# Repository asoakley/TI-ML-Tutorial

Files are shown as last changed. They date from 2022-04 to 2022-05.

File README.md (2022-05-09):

# TI-ML-Tutorial
<html>
<body>
<h1>TI Machine Learning Robotics</h1>
<h3>Tutorial repository for TI-RSLK MAX Machine Learning used for NC State ECE Senior Design Fall 2021-Spring 2022</h3>
<ul>
    <li>PCB folder contains Eagle CAD files for the custom PCB schematic file as well as the board file. It also includes the necessary gerbers and libraries needed to recreate the custom sensors PCB</li>
    <ul>
        <li>Eagle Libraries contains the libraries needed to recreate our schematic and board</li>
        <li>PCB Gerbers are the gerber files that can be sent to a manufacturer for printing</li>
    </ul>
    <li>libraries folder contains the libraries used in Arduino IDE to get the MSP432 microcontroller and the RSLK MAX to function. 
    It also contains two pretrained Edge Impulse libraries that we have tested for both Terrrain Recognition and Keyword Recognition</li>
    <li>prediction folder contains the Arduino code for running edge impulse models. 
    It contains code for both Audio and Accelerometer Machine Learning as well as a template code for any sensors you would like to have.</li>
    <li>test and training folder contains Arduino code to sample accelerometer and/or audio data of the RSLK MAX</li>
</ul>
    
<p> Check out our Hackster.io pages for
<a href="https://www.hackster.io/nc-state-ece-design-team-3-fall-2021-spring-2022/ti-rslk-machine-learning-robotics-terrain-recognition-a90367">Terrain Recognition</a> and 
<a href="https://www.hackster.io/nc-state-ece-design-team-3-fall-2021-spring-2022/ti-rslk-machine-learning-robotics-keyword-recognition-d96755">Keyword Recognition</a>!
</p>
</body>
</html>

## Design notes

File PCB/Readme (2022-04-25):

This will contain files that can be used to manufacture and assemble you own PCB

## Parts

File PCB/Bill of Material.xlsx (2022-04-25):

BoM
Custom PCB Bill of Materials
Component | Parts Number | Footprint | Quantity | Vendor | Link
2x10 Female Header with Extended Pins | SSQ-110-23-L-D | Pitch 2.54mm | 2 | Mouser | https://www.mouser.com/ProductDetail/Samtec/SSQ-110-23-L-D?qs=%252BZP6%2F%252BtExtARWAN2o%252BG5sw%3D%3D
BMI160 Breakout Board | GY-BMI160 |  | 1 | Amazon | https://www.amazon.com/UMLIFE-GY-BMI160-Accelerometer-Gyroscope-Acceleration/dp/B09BQTP8SN
Microphone | POM-2242P-C33-R |  | 1 | Mouser | https://www.mouser.com/ProductDetail/PUI-Audio/POM-2242P-C33-R?qs=%252BDOaWfEBs1NMmnxc1pdyNQ%3D%3D
Op Amp | TLV2760IDBVTG4 |  | 1 | Mouser | https://www.mouser.com/ProductDetail/Texas-Instruments/TLV2760IDBVTG4?qs=Fg5TsMy7H4tOABiS42YeFQ%3D%3D
51 pF Capacitor | CC0805JRNPO9BN510 | 805 | 1 | Mouser | https://www.mouser.com/ProductDetail/YAGEO/CC0805JRNPO9BN510?qs=57cj7OiSijnFc2K4M5Y88A%3D%3D
0.015 uF Capacitor | CC0805KRX7R9BB153 | 805 | 1 | Mouser | https://www.mouser.com/ProductDetail/YAGEO/CC0805KRX7R9BB153?qs=AgBp2OyFlx%2FPOw7ZPkNw5g%3D%3D
0.1 uF Capacitor | CL21F104ZAANNNC | 805 | 1 | Mouser | https://www.mouser.com/ProductDetail/Samsung-Electro-Mechanics/CL21F104ZAANNNC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
0.15 uF Capacitor | CL21B474KAFNNNE | 805 | 1 | Mouser | https://www.mouser.com/ProductDetail/YAGEO/CC0805KRX7R8BB154?qs=7s%252B3O6pAiyBZMZQviySFxQ%3D%3D
0.47 uF Capacitor | CL31B475KOHNNNE | 805 | 2 | Mouser | https://www.mouser.com/ProductDetail/Samsung-Electro-Mechanics/CL21B474KAFNNNE?qs=349EhDEZ59pAOdNiq9aGMQ%3D%3D
4.7 uF Capacitor | CL31B475KOHNNNE | 805 | 2 | Mouser | https://www.mouser.com/ProductDetail/Samsung-Electro-Mechanics/CL31B475KOHNNNE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
470 Ohm Resistor | RC1206FR-07470RL | 1206 | 1 | Mouser | https://www.mouser.com/ProductDetail/YAGEO/RC1206FR-07470RL?qs=sGAEpiMZZMtlubZbdhIBIKjip0x71NJPKLhM6znFk4g%3D
820 Ohm Resistor | RC1206FR-07820RL | 1206 | 2 | Mouser | https://www.mouser.com/ProductDetail/YAGEO/RC1206FR-07820RL?qs=rU22MploB9qblXEL9hXxYA%3D%3D
3k Ohm Resistor | RC1206FR-073KL | 1206 | 1 | Mouser | https://www.mouser.com/ProductDetail/YAGEO/RC1206FR-073KL?qs=bz%2FLPVPAsTIWQzAcjuMv7A%3D%3D
8.2k Ohm Resistor | RC1206FR-078K2L | 1206 | 1 | Mouser | https://www.mouser.com/ProductDetail/YAGEO/RC1206FR-078K2L?qs=2UBm2ZpWbY7NiTYWn65QRA%3D%3D
47k Ohm Resistor | RC1206FR-0747KL | 1206 | 1 | Mouser | https://www.mouser.com/ProductDetail/YAGEO/RC1206FR-0747KL?qs=fiyQ2z0a5emCDAPrRKyH9Q%3D%3D
51k Ohm Resistor | RC1206FR-0751KL | 1206 | 1 | Mouser | https://www.mouser.com/ProductDetail/YAGEO/RC1206FR-0751KL?qs=sGAEpiMZZMtlubZbdhIBIKjip0x71NJPyUVd7sO0YBM%3D
200k Ohm Resistor | AF1206FR-07200KL | 1206 | 1 | Mouser | https://www.mouser.com/ProductDetail/YAGEO/AF1206FR-07200KL
Optional
2x3 Male Header | M20-9980346 | Pitch 2.54mm | 1 | Mouser | https://www.mouser.com/ProductDetail/Harwin/M20-9980346?qs=%252Bk6%2F5FB6qrmHk2P20oz3FA%3D%3D
2x6 Male Header | 10123427-406001LF | Pitch 2.54mm | 1 | Mouser | https://www.mouser.com/ProductDetail/TE-Connectivity/5-146257-6?qs=bwpFY26eRVePjiL6RaoxRg%3D%3D

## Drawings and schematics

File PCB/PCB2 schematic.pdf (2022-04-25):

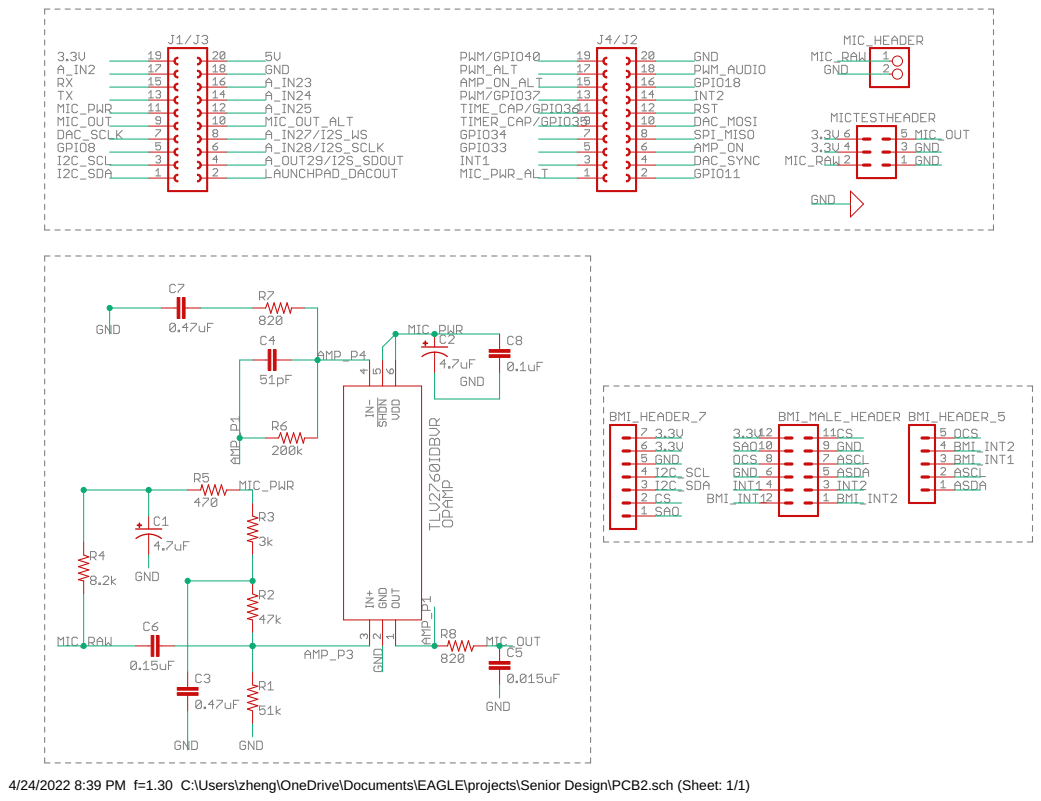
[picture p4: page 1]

4/24/2022 8:39 PM f=1.30 C:\Users\zheng\OneDrive\Documents\EAGLE\projects\Senior Design\PCB2.sch (Sheet: 1/1)

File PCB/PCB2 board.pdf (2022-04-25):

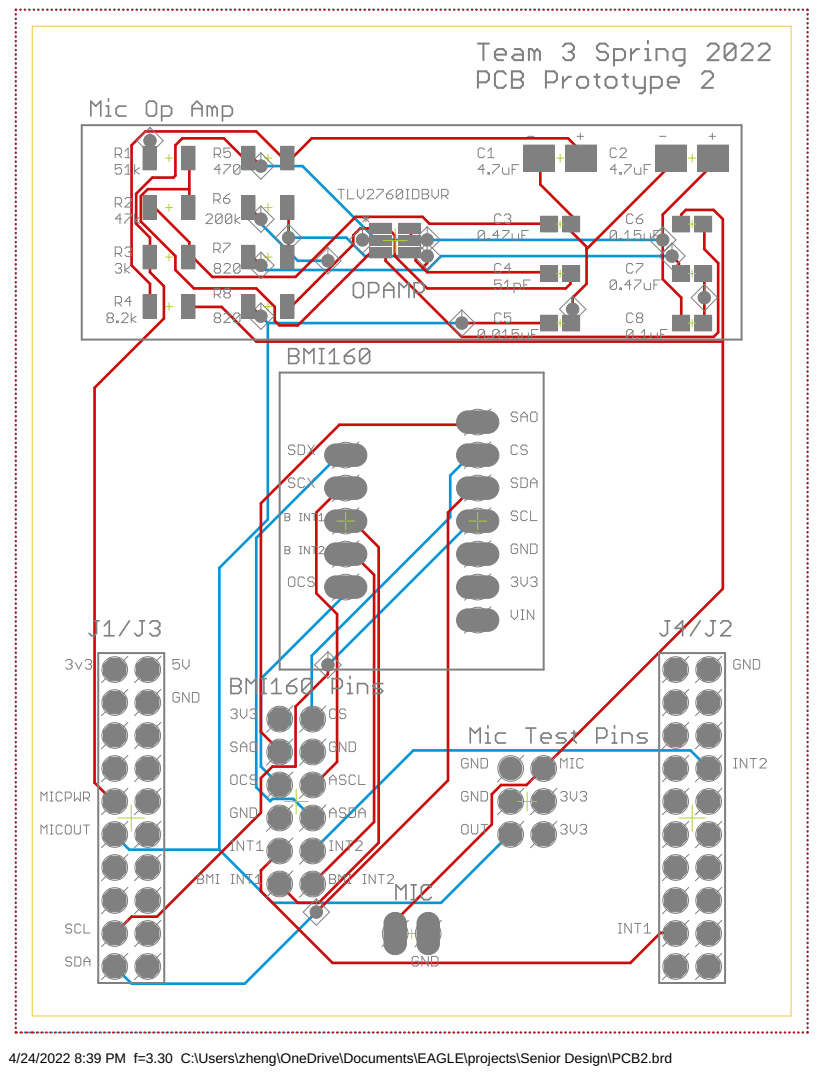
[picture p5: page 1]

4/24/2022 8:39 PM f=3.30 C:\Users\zheng\OneDrive\Documents\EAGLE\projects\Senior Design\PCB2.brd

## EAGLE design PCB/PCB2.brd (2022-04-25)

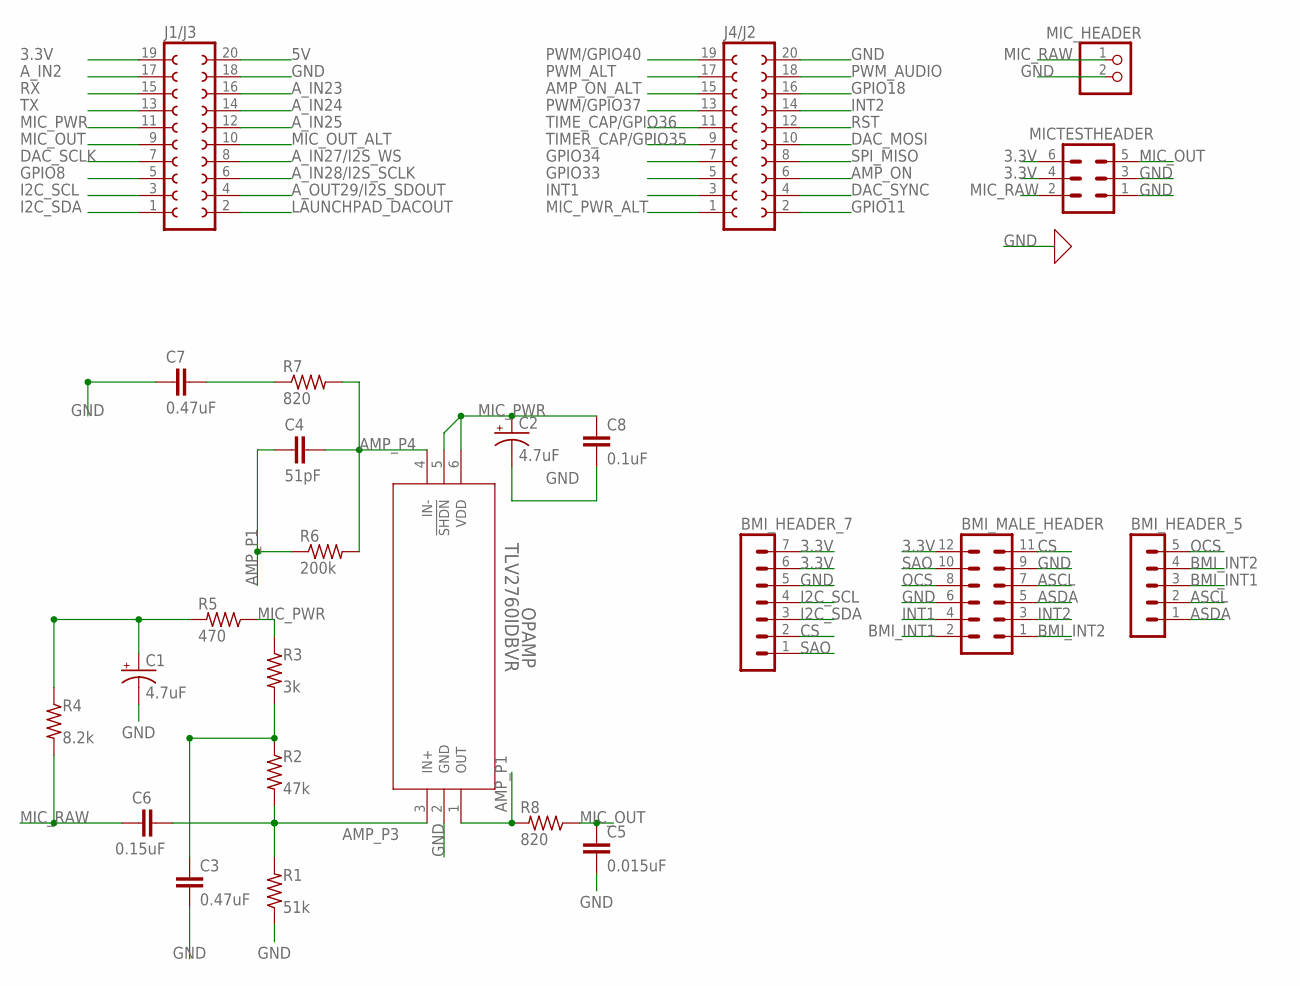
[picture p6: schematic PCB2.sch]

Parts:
BMI_HEADER_5: MA05-1
BMI_HEADER_7: MA07-1
BMI_MALE_HEADER: MA06-2
C1, C2: 4.7uF; B/3528-21W
C3, C7: 0.47uF; C0603
C4: 51pF; C0603
C5: 0.015uF; C0603
C6: 0.15uF; C0603
C8: 0.1uF; C0603
J1/J3, J4/J2: FE10-2W
MICTESTHEADER: MA03-2
MIC_HEADER: PINHD-1X2; 1X02
OPAMP: TLV2760IDBVR; DBV6
R1: 51k; MINI_MELF-0204R
R2: 47k; MINI_MELF-0204R
R3: 3k; MINI_MELF-0204R
R4: 8.2k; MINI_MELF-0204R
R5: 470; MINI_MELF-0204R
R6: 200k; MINI_MELF-0204R
R7, R8: 820; MINI_MELF-0204R

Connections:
3.3V: BMI_HEADER_7.6, BMI_HEADER_7.7, BMI_MALE_HEADER.12, J1/J3.19, MICTESTHEADER.4, MICTESTHEADER.6
5V: J1/J3.20
AMP_ON: J4/J2.6
AMP_ON_ALT: J4/J2.15
AMP_P1: C4.2, OPAMP.1 (OUT), R6.1, R8.2
AMP_P3: C6.2, OPAMP.3 (IN+), R1.2, R2.2
AMP_P4: C4.1, OPAMP.4 (IN-), R6.2, R7.2
ASCL: BMI_HEADER_5.2, BMI_MALE_HEADER.7
ASDA: BMI_HEADER_5.1, BMI_MALE_HEADER.5
A_IN2: J1/J3.17
A_IN23: J1/J3.16
A_IN24: J1/J3.14
A_IN25: J1/J3.12
A_IN27/I2S_WS: J1/J3.8
A_IN28/I2S_SCLK: J1/J3.6
A_OUT29/I2S_SDOUT: J1/J3.4
BMI_INT1: BMI_HEADER_5.3, BMI_MALE_HEADER.2
BMI_INT2: BMI_HEADER_5.4, BMI_MALE_HEADER.1
CS: BMI_HEADER_7.2, BMI_MALE_HEADER.11
DAC_MOSI: J4/J2.10
DAC_SCLK: J1/J3.7
DAC_SYNC: J4/J2.4
GND: BMI_HEADER_7.5, BMI_MALE_HEADER.6, BMI_MALE_HEADER.9, C1.-, C2.-, C3.2, C5.2, C7.2, C8.2, J1/J3.18, J4/J2.20, MICTESTHEADER.1, MICTESTHEADER.3, MIC_HEADER.2, OPAMP.2 (GND), R1.1
GPIO8: J1/J3.5
GPIO11: J4/J2.2
GPIO18: J4/J2.16
GPIO33: J4/J2.5
GPIO34: J4/J2.7
I2C_SCL: BMI_HEADER_7.4, J1/J3.3
I2C_SDA: BMI_HEADER_7.3, J1/J3.1
INT1: BMI_MALE_HEADER.4, J4/J2.3
INT2: BMI_MALE_HEADER.3, J4/J2.14
LAUNCHPAD_DACOUT: J1/J3.2
MIC_OUT: C5.1, J1/J3.9, MICTESTHEADER.5, R8.1
MIC_OUT_ALT: J1/J3.10
MIC_PWR: C2.+, C8.1, J1/J3.11, OPAMP.5 (!SHDN), OPAMP.6 (VDD), R3.1, R5.1
MIC_PWR_ALT: J4/J2.1
MIC_RAW: C6.1, MICTESTHEADER.2, MIC_HEADER.1, R4.2
unnamed: C3.1, R2.1, R3.2
unnamed: C1.+, R4.1, R5.2
unnamed: C7.1, R7.1
OCS: BMI_HEADER_5.5, BMI_MALE_HEADER.8
PWM/GPIO37: J4/J2.13
PWM/GPIO40: J4/J2.19
PWM_ALT: J4/J2.17
PWM_AUDIO: J4/J2.18
RST: J4/J2.12
RX: J1/J3.15
SAO: BMI_HEADER_7.1, BMI_MALE_HEADER.10
SPI_MISO: J4/J2.8
TIMER_CAP/GPIO35: J4/J2.9
TIME_CAP/GPIO36: J4/J2.11
TX: J1/J3.13

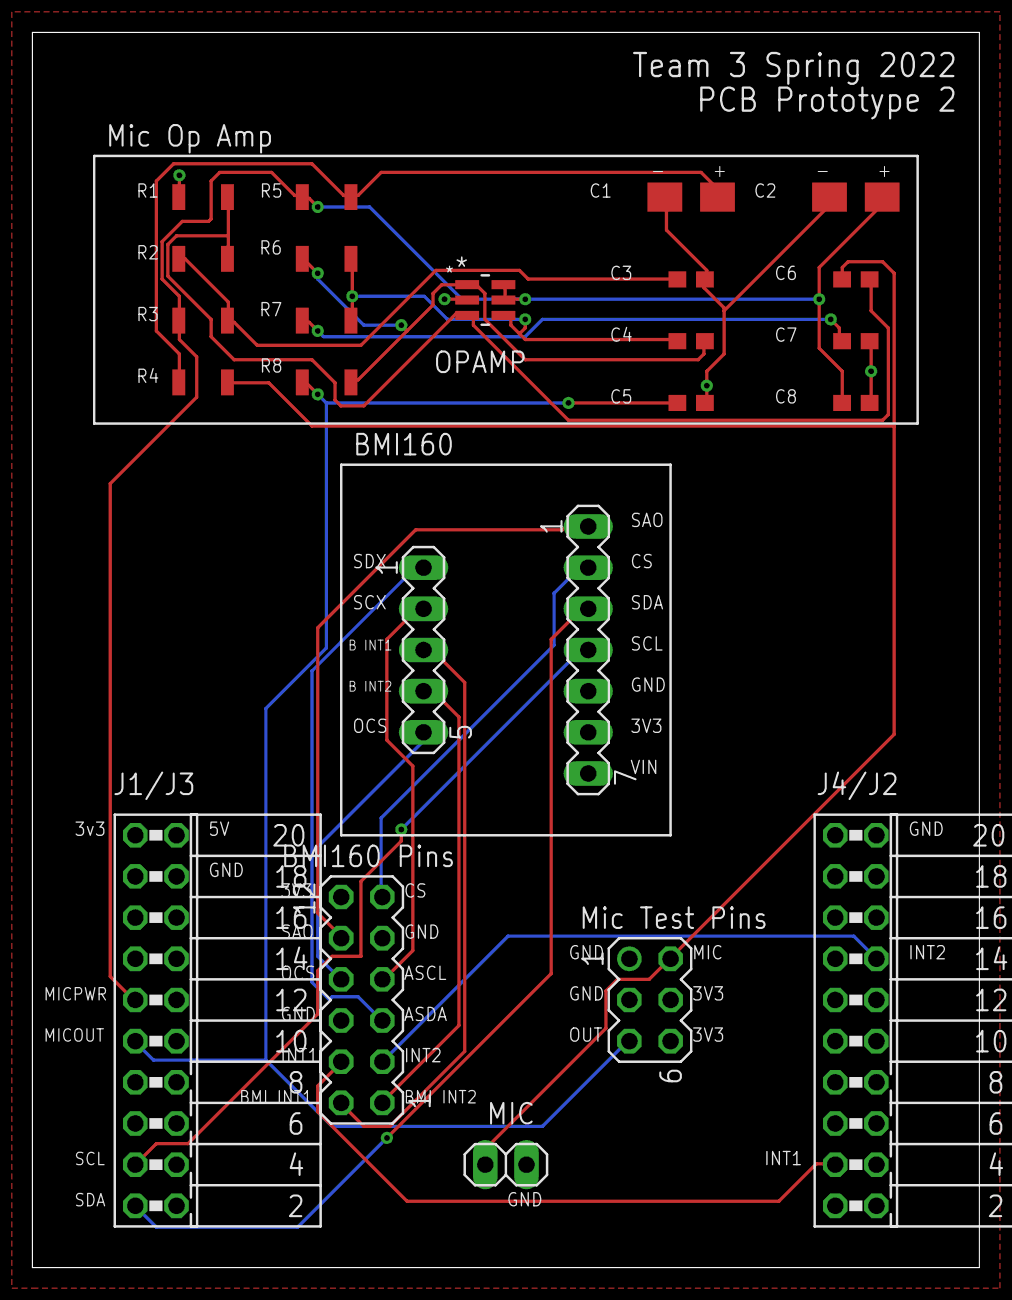
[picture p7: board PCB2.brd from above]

Board: 2 copper layers, 58.4 x 76.2 mm, 24 parts (0 on the bottom side), 22 nets.

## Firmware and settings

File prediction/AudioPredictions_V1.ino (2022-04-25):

// North Carolina State University ECE Senior Design Team 3 Spring 2022
// April 25, 2022
// TI Machine Learning Robotics
// AudioPredictions_V1
// Keyword spotting for Drive and Clockwise
// Available at https://github.com/asoakley/TI-ML-Tutorial

#include <TI-ML-Audio-Classification_inferencing.h>

// RSLK and accelerometer libraries
#include <SimpleRSLK.h>

#define MIC_PWR   5   // RLSK Pin P4.1, BoosterPack(Energia) Pin J1-5
#define MIC_OUT   6   // RSLK Pin P4.3, BoosterPack(Energia) Pin J1-6

// Private variables
static bool debug_nn = false; // Set this to true to see e.g. features generated from the raw signal

// Allocate a buffer here for the values we'll read from the IMU
float buffer[EI_CLASSIFIER_DSP_INPUT_FRAME_SIZE] = { 0 };

#define SAMPLE_PERIOD    1    // 1 ms, 1000 Hz

void setup() {
  
  setupRSLK();
  enableMotor(BOTH_MOTORS);
  setMotorSpeed(BOTH_MOTORS,0);

  // Initialize LED pins as outputs
  pinMode(LED_FR_PIN, OUTPUT); 
  pinMode(LED_FL_PIN, OUTPUT); 
  pinMode(LP_RED_LED_PIN, OUTPUT);
  pinMode(LP_RGB_LED_RED_PIN, OUTPUT);
  pinMode(LP_RGB_LED_BLUE_PIN, OUTPUT); 
  pinMode(LP_RGB_LED_GREEN_PIN, OUTPUT);

  pinMode(MIC_PWR, OUTPUT);
  digitalWrite(MIC_PWR, HIGH); // Provide power to the mic
  pinMode(MIC_OUT, INPUT);     // Set the output of the mic to an analog input
  
  analogReadResolution(14);

  Serial.begin(115200); // initialize Serial communication
  while (!Serial);      // wait for the serial port to open

  digitalWrite(LP_RGB_LED_BLUE_PIN, HIGH);
  delay(500);

  if (EI_CLASSIFIER_RAW_SAMPLES_PER_FRAME != 1) {
    ei_printf("ERR: EI_CLASSIFIER_RAW_SAMPLES_PER_FRAME should be equal to 1 (the one audio pin)\n");
    return;
  }
  digitalWrite(LP_RGB_LED_BLUE_PIN, LOW);
}

void getAudio() {
  int audio;
  for (int i = 0; i < EI_CLASSIFIER_DSP_INPUT_FRAME_SIZE; i += 1) {
    // Analog read mic pin
    audio = analogRead(MIC_OUT);
    // Add audio data to buffer
    buffer[i] = audio;
    delay(SAMPLE_PERIOD);
  }
}

void audioPredict() {
  // Get audio data
  Serial.println("\nSampling...");
  // RGB LED lights red while sampling data
  digitalWrite(LP_RGB_LED_RED_PIN, HIGH);
  getAudio();
  digitalWrite(LP_RGB_LED_RED_PIN, LOW);

  // Turn the raw buffer in a signal which we can the classify
  signal_t signal;
  int err = numpy::signal_from_buffer(buffer, EI_CLASSIFIER_DSP_INPUT_FRAME_SIZE, &signal);
  if (err != 0) {
    ei_printf("Failed to create signal from buffer (%d)\n", err);
    return;
  }

  // Run the classifier
  ei_impulse_result_t result = { 0 };

  err = run_classifier(&signal, &result, debug_nn);
  if (err != EI_IMPULSE_OK) {
    ei_printf("ERR: Failed to run classifier (%d)\n", err);
    return;
  }

  // Print the predictions
  float check = 0.0;
  String pred = "";
  ei_printf("Predictions ");
  ei_printf("(DSP: %d ms., Classification: %d ms., Anomaly: %d ms.): \n",
            result.timing.dsp, result.timing.classification, result.timing.anomaly);
  for (size_t ix = 0; ix < EI_CLASSIFIER_LABEL_COUNT; ix++) {
    ei_printf("    %s: %.5f\n", result.classification[ix].label, result.classification[ix].value);
    if (result.classification[ix].value > check) {
      pred = result.classification[ix].label;
      check = result.classification[ix].value;
    }
  }
///////////////// Edit this section according to your model classes /////////////////
  setMotorSpeed(BOTH_MOTORS,15);
  // Move motors for set time when detecting motion commands
  // If a command is not detected, program immediately runs back through loop
  if (pred == "Drive"){
    setMotorDirection(BOTH_MOTORS, MOTOR_DIR_FORWARD);
    delay(1000);
  }
  if (pred == "Clockwise"){
    setMotorDirection(LEFT_MOTOR, MOTOR_DIR_FORWARD);
    setMotorDirection(RIGHT_MOTOR, MOTOR_DIR_BACKWARD);
    delay(1000);
  }
  setMotorSpeed(BOTH_MOTORS,0);
/////////////////////////////////////////////////////////////////////////////////////
}

void loop(){
  // Run audio ML algorithm
  audioPredict();
}

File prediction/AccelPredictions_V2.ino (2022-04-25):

// North Carolina State University ECE Senior Design Team 3 Spring 2022
// April 25, 2022
// TI Machine Learning Robotics
// AccelPredictions_V2
// Continuous forward drive accelerometer classification
// Available at https://github.com/asoakley/TI-ML-Tutorial


// Change this include to match the name of your imported Edge Impulse Arduino library
#include <TI-ML-Terrain-Recognition_inferencing.h>

// RSLK and accelerometer libraries
#include <SimpleRSLK.h>
#include <BMI160Gen.h>

const int bmi160_i2c_addr = 0x69;
const int bmi160_interrupt_pin = 17;

volatile int state = 0;   // 0 -> OFF, 1 -> RUN ALGORITHM
volatile int back = 0;    // If 1, robot will back up after each time running

// Private variables
static bool debug_nn = false; // Set this to true to see e.g. features generated from the raw signal

// Allocate a buffer here for the values we'll read from the IMU
float buffer[EI_CLASSIFIER_DSP_INPUT_FRAME_SIZE] = { 0 };

#define SAMPLE_PERIOD    20 // 0.02 seconds, 50 Hz

void setup() {
  
  setupRSLK();
  enableMotor(BOTH_MOTORS);
  setMotorSpeed(BOTH_MOTORS,0);
  setMotorDirection(BOTH_MOTORS, MOTOR_DIR_FORWARD);

  // Initialize LED pins as outputs
  pinMode(LED_FR_PIN, OUTPUT); 
  pinMode(LED_FL_PIN, OUTPUT); 
  pinMode(LP_RED_LED_PIN, OUTPUT);
  pinMode(LP_RGB_LED_RED_PIN, OUTPUT);
  pinMode(LP_RGB_LED_BLUE_PIN, OUTPUT); 
  pinMode(LP_RGB_LED_GREEN_PIN, OUTPUT);

  // Initialize LaunchPad buttons as inputs
  pinMode(LP_S1_PIN, INPUT_PULLUP);
  pinMode(LP_S2_PIN, INPUT_PULLUP);
  attachInterrupt(digitalPinToInterrupt(LP_S1_PIN),SW1_ISR, RISING);
  attachInterrupt(digitalPinToInterrupt(LP_S2_PIN),SW2_ISR, RISING);

  Serial.begin(115200); // initialize Serial communication
  while (!Serial);    // wait for the serial port to open

  // Initialize accelerometer
  Serial.println("Initializing IMU device...");
  BMI160.begin(BMI160GenClass::I2C_MODE, bmi160_i2c_addr, bmi160_interrupt_pin);
  uint8_t dev_id = BMI160.getDeviceID();
  Serial.print("DEVICE ID: ");
  Serial.println(dev_id, HEX);

  // Set the accelerometer range to 4G
  BMI160.setAccelerometerRange(4); 
  Serial.println("Initializing IMU device...done.");

  // Wait two seconds before starting
  delay(2000);

  if (EI_CLASSIFIER_RAW_SAMPLES_PER_FRAME != 3) {
    ei_printf("ERR: EI_CLASSIFIER_RAW_SAMPLES_PER_FRAME should be equal to 3 (the 3 sensor axes)\n");
    return;
  }
}

void SW2_ISR(){
  state = !state;
  if (state == 0) {
    setMotorSpeed(BOTH_MOTORS,0);
  }
}

void SW1_ISR(){
  back = !back;
}

void getAcceleration() {
  int xRaw, yRaw, zRaw;
  float x, y, z;
  for (int i = 0; i < EI_CLASSIFIER_DSP_INPUT_FRAME_SIZE; i += 3) {
    BMI160.readAccelerometer(xRaw, yRaw, zRaw);
    x = convertRawAccel(xRaw);
    y = convertRawAccel(yRaw);
    z = convertRawAccel(zRaw);
    // Add accelerometer data to buffer
    buffer[i + 0] = x;
    buffer[i + 1] = y;
    buffer[i + 2] = z;
    delay(SAMPLE_PERIOD);
  }
}

float convertRawAccel(int gRaw) {
  // since we are using 4G range
  // -4 maps to a raw value of -32768
  // +4 maps to a raw value of 32767
  float g = (gRaw * 40) / 32768.0;
  return g;
}

void predict() {
  // Get accelerometer data
  Serial.println("Sampling...");
  getAcceleration();

  // Turn the raw buffer in a signal which we can the classify
  signal_t signal;
  int err = numpy::signal_from_buffer(buffer, EI_CLASSIFIER_DSP_INPUT_FRAME_SIZE, &signal);
  if (err != 0) {
    ei_printf("Failed to create signal from buffer (%d)\n", err);
    return;
  }

  // Run the classifier
  ei_impulse_result_t result = { 0 };

  err = run_classifier(&signal, &result, debug_nn);
  if (err != EI_IMPULSE_OK) {
    ei_printf("ERR: Failed to run classifier (%d)\n", err);
    return;
  }

  // Print the predictions
  float check = 0.0;
  String pred = "";
  ei_printf("Predictions ");
  ei_printf("(DSP: %d ms., Classification: %d ms., Anomaly: %d ms.): \n",
            result.timing.dsp, result.timing.classification, result.timing.anomaly);
  for (size_t ix = 0; ix < EI_CLASSIFIER_LABEL_COUNT; ix++) {
    ei_printf("    %s: %.5f\n", result.classification[ix].label, result.classification[ix].value);
    if (result.classification[ix].value > check) {
      pred = result.classification[ix].label;
      check = result.classification[ix].value;
    }
  }
  
  // Turn off RGB LED
  digitalWrite(LP_RGB_LED_RED_PIN, LOW);
  digitalWrite(LP_RGB_LED_BLUE_PIN, LOW);
  digitalWrite(LP_RGB_LED_GREEN_PIN, LOW);
  
///////////////////// Display predictions with RGB LED /////////////////////
  if (pred == "Carpet"){
    digitalWrite(LP_RGB_LED_RED_PIN, HIGH);
    digitalWrite(LP_RGB_LED_GREEN_PIN, HIGH);
    digitalWrite(LP_RGB_LED_BLUE_PIN, HIGH);
  }
  if (pred == "Turf"){
    digitalWrite(LP_RGB_LED_GREEN_PIN, HIGH);
  }
  if (pred == "Foam") {
    digitalWrite(LP_RGB_LED_BLUE_PIN, HIGH);
  }
  if (pred == "Wood") {
    digitalWrite(LP_RGB_LED_RED_PIN, HIGH);
    digitalWrite(LP_RGB_LED_BLUE_PIN, HIGH);
  }
  if (pred == "Brick") {
    digitalWrite(LP_RGB_LED_RED_PIN, HIGH);
  }
////////////////////////////////////////////////////////////////////////////
}

void loop(){
  // Robot is waiting to start
  if (state == 0) {
    digitalWrite(LED_FR_PIN, HIGH);
    digitalWrite(LED_FL_PIN, HIGH);
    digitalWrite(LP_RGB_LED_RED_PIN, LOW);
    digitalWrite(LP_RGB_LED_BLUE_PIN, LOW);
    digitalWrite(LP_RGB_LED_GREEN_PIN, LOW);
    setMotorSpeed(BOTH_MOTORS,0);
  }
  
  // Run accelerometer ML algorithm
  if (state == 1) {
    digitalWrite(LED_FR_PIN, LOW);
    digitalWrite(LED_FL_PIN, LOW);
    setMotorSpeed(BOTH_MOTORS,15);
    predict();
    if (back == 1) {
      setMotorDirection(BOTH_MOTORS, MOTOR_DIR_BACKWARD);
      delay(1000);
      setMotorDirection(BOTH_MOTORS, MOTOR_DIR_FORWARD);
    }
  }
}

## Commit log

2022-04-19 Accelerometer Sampling Code
2022-04-19 Device Support and Inferencing Libraries
2022-04-25 Template for uploading sensor data to Edge Impulse
2022-04-25 Create BoM for custom PCB
